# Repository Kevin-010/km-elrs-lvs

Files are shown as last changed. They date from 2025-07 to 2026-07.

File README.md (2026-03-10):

# km-elrs-lvs
A 2.4ghz ExpressLRS-compatible PWM receiver with integrated cell monitoring. KiCad project and related files.

This was created as a personal project to offset having used propreitary radio systems for several years prior (the previous truely usable open standard being PPM/FM): Suddenly (from my perspective) the community has an open source radio system and it also happens to be the best performing? I had to have one, so I made one.
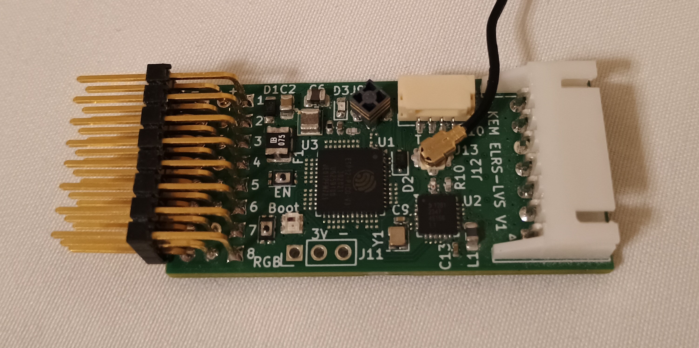
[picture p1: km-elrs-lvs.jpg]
receiver photo

Specs:
- ESP32 (PICO-V3) processor
- SX1280/1281 telemetry radio (direct 1x1, +12.5dBm) anything fancier isn't necessary for outdoor los on a small/medium plane (but more importantly would have been less likely to succeed when hand built)
- 1-3s (3.0-17v) input/servo power, with external brownout detector (the esp builtin one is problematic)
- 8 Channel PWM output, on standard servo pin headers
- JST GH CRSF/Serial/programming connector (similar to radiomaster cables)
- 7 channel voltage sense connector, measuring -5 to +35v (for 2-6s standard lipo balance plugs)

This not a beginner soldering project.  It is built similarly to most RC hardware - double sided with (almost) minimal compoent sizes crammed as close as possible to each other to save size and weight.  That said, it can be assembled by hand - I had no significant issues, although I recommend using at least a paste stencil.

The Wifi (ceramic tower) and ELRS (u.fl) footprints are made more interchangable for experimental purposes. As of version 1, the CRSF connector pinout is non-standard, due to an oversight (I thought it was downside up when I copied it from radiomaster's cable example). There are many test/cut points that could be removed to save space on a version 2 (none of the cut points were necessary, which is a great success, and why it's stuck at the first version)

Version 2 (Not yet tested) removes the test points, moves all components to the front side, fixes the CRSF pinout to match radiomaster cables, and uses larger clearances to allow a slightly cheaper pcb process.

Despite this project being built mostly a cathartic exercise, this has the unique (as of writing) feature of monitoring individual lithium cell voltages integrated into the receiver. This is the most common telemetry item I personally use on aircraft - Having it integrated, in addition to the weight/size reduction, is intended to increase the durability of combat aircraft (on which the cell sensor and interconnect is a common failure point), and otherwise reduce the chance for an aircraft to be missing its sensor. The cost is also theoretically lower than the equivalent two devices, since this only requires hardware integrated into the receiver cpu, but i'd have to sell them for that to actually make sense. This feature currently requires a small amount of custom software, see related repository (TODO LINK HERE).

Some footprints are Borrowed from other public hardware examples:
- https://github.com/crteensy/ELRS-8285-1280-5xPWM.git 
- https://github.com/AnyLeaf/elrs-hardware.git

To build firmware images for this and similar unsupported hardware, one can add an entry to ExpressLRS/targets/targets.json , after which platformio or elrs configurator in local mode can be used.
```
"km_lvs": {
                "product_name": "Kevin LVS 2.4GHz 8xPWM RX",
                "lua_name": "KM LVS",
                "layout_file": "elrs-lvs.json",
                "upload_methods": ["uart", "wifi"],
                "min_version": "3.3.0",
                "platform": "esp32",
                "firmware": "Unified_ESP32_2400_RX"
            },
```

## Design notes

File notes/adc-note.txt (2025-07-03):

            "km_lvs": {
                "product_name": "Kevin LVS 2.4GHz 8xPWM RX",
                "lua_name": "KM LVS",
                "layout_file": "elrs-lvs.json",
                "upload_methods": ["uart", "wifi"],
                "min_version": "3.3.0",
                "platform": "esp32",
                "firmware": "Unified_ESP32_2400_RX"
            },

Adafruit 3x4 Right Angle Male Header - 4 Pack [ADA816] 
https://www.abelectronics.co.uk/p/73/24-pin-8-x-3-right-angle-header

samtec TSW-150-25-F-T-RA
(3x4) TSW-104-25-G-T-RA

adc
real	vs5	lvs6	sim
-6		142	-20.058
-5		142	58.43
-4		172	136.919
-3		248	215.407
-2		327	293.895
-1		405	372.384
0		480	450.872
nc		520	489.274
1		560	529.36
2		640	607.848
3	649	719	686.337
3.3	724		709.884
4	796	797	764.826
5	874	876	843.314
6	953	954	921.802
7	1036	1037	1000
8	1116	1117	1079
9	1195	1196	1157
10	1274	1275	1236
11	1353	1354	1314
12	1438	1438	1393
13	1516	1516	1471
14	1595	1594	1550
15	1671	1672	1628
16	1751	1750	1707
17	1837	1833	1785
18		1910	1864
19		1987	1942
20		2066	2021
21		2143	2099
22		2221	2178
23		2305	2256
24		2387	2335
25		2466	2413
26		2539	2492
27		2611	2570
28		2685	2649
29		2760	2727
30		2835	2806
31		2912	2884

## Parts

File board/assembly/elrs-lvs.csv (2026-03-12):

Reference | Value | Footprint | Qty | Part | Manufacturer | DNP | Alt part number | Digikey | LCSC | Mouser
C4 | 10u | Capacitor_SMD:C_0402_1005Metric | 1 | CL05A106MQ5NUNC | Samsung |  |  | https://www.digikey.com/en/products/detail/samsung-electro-mechanics/CL05A106MQ5NUNC/3887109 | C15525
C7,C8 | 10n | Capacitor_SMD:C_0402_1005Metric | 2 | CL05B103KB5NNNC | Samsung |  |  | https://www.digikey.com/en/products/detail/samsung-electro-mechanics/CL05B103KB5NNNC/3886686 | C15195
C9 | 1n | Capacitor_SMD:C_0402_1005Metric | 1 | KGM05AR71H102KN | Kyocera AVX |  |  | https://www.digikey.com/en/products/detail/kyocera-avx/KGM05AR71H102KN/3661149 | C2168479
C13 | 470n, 10V | Capacitor_SMD:C_0402_1005Metric | 1 | CL05A474KP5NNNC | Samsung |  |  | https://www.digikey.com/en/products/detail/samsung-electro-mechanics/CL05A474KP5NNNC/3886831 | C47339
D4 | WS2812B 2020 | Anyleaf_Shared:LED-WS2812B | 1 | WS2812B-2020 | Multiple |  |  | 1528-4684-ND (Adafruit 4684) | C965555
J13 | U.FL | elrs-lvs:U.FL_Hirose_U.FL-R-SMT-1_Vertical_Molex_47948-0001 | 1 | U.FL-R-SMT-1(80) | Hirose Electric |  |  |  | C88374
L1 | 15u | Inductor_SMD:L_0805_2012Metric | 1 | MLZ2012M150W | TDK |  |  | https://www.digikey.com/en/products/detail/tdk/MLZ2012M150WT000/2465154 | C486333 | 810-MLZ2012M150WT000
U2 | SX1281 | Package_DFN_QFN:QFN-24-1EP_4x4mm_P0.5mm_EP2.6x2.6mm | 1 | SX1281IMLTRT | Semtech |  |  | SX1281IMLTRTTR-ND | C2151551 | 947-SX1281IMLTRT
U3 | TPSM82901SISR | elrs-lvs:uSIP11_SIS_TEX | 1 | TPSM82901SISR | Texas Instruments |  |  | https://www.digikey.com/en/products/detail/texas-instruments/TPSM82901SISR/17394938 | C6290581
U4 | 2450FM07D0034T | Anyleaf_Shared:2450FM07D0034 | 1 | 2450FM07D0034T | Johanson |  | 2450FM07A0029T | 712-1654-2-ND | C2651081 | 609-2450FM07D0034T
Y1 | 52Mhz TCXO | Crystal:Crystal_SMD_2016-4Pin_2.0x1.6mm | 1 | ECS-TXO-20CSMV4-520-AN-TR | ECS Inc. |  |  | 50-ECS-TXO-20CSMV4-520-AN-TRCT-ND | C22434896
C3,C10,C11,C12,C14,C15,C16,C17,C18,C19,C20,C21 | 100n | Capacitor_SMD:C_0402_1005Metric | 12 | CL05A104KA5NNNC | Samsung |  |  | https://www.digikey.com/en/products/detail/samsung-electro-mechanics/CL05A104KA5NNNC/3886701 | C100072
J10 | CF/Prog | Connector_JST:JST_GH_SM04B-GHS-TB_1x04-1MP_P1.25mm_Horizontal | 1 | SM04B-GHS-TB | JST |  |  | https://www.digikey.com/en/products/detail/jst-sales-america-inc/SM04B-GHS-TB/807788 | C189895
D3 | Power | LED_SMD:LED_0603_1608Metric | 1 | LY Q976.01-Q1R2-36-1 | osram |  |  | https://www.digikey.com/en/products/detail/ams-osram-usa-inc/LY-Q976-01-Q1R2-36-1/21556496 | C20562575
F1 | 500ma | Capacitor_SMD:C_1210_3225Metric | 1 | SMD1210B075TF/24 | Yageo |  |  | https://www.digikey.com/en/products/detail/yageo/SMD1210B075TF-24/15212934 | C634245
R1,R13 | 10k | Resistor_SMD:R_0402_1005Metric | 2 | AC0402JR-0710KL | Yageo |  |  | https://www.digikey.com/en/products/detail/yageo/AC0402JR-0710KL/5895571 | C144731
R14 | 470 | Resistor_SMD:R_0402_1005Metric | 1 | AC0402JR-07470RL | Yageo |  |  | https://www.digikey.com/en/products/detail/yageo/AC0402JR-07470RL/5895678 | C144711
R2 | 40.2k | Resistor_SMD:R_0402_1005Metric | 1 | AC0402FR-0740K2L | Yageo |  |  | https://www.digikey.com/en/products/detail/yageo/AC0402FR-0740K2L/5895346 | C144760
R3,R15,R16,R17,R18,R19,R20,R21,R22,R47,R48 | 100 | Resistor_SMD:R_0402_1005Metric | 11 | AC0402JR-07100RL | Yageo |  |  | https://www.digikey.com/en/products/detail/yageo/AC0402JR-07100RL/5895570 | C138288
R10,R31,R32,R33,R34,R35,R36,R37,R38 | 270k | Resistor_SMD:R_0402_1005Metric | 9 | RC0402FR-07270KL | Yageo |  |  | https://www.digikey.com/en/products/detail/yageo/RC0402FR-07270KL/726575 | C163475
R23,R24,R25,R26,R27,R28,R29,R30 | 470k | Resistor_SMD:R_0402_1005Metric | 8 | RC0402DR-07470KL | Yageo |  |  | https://www.digikey.com/en/products/detail/yageo/RC0402DR-07470KL/5917402 | C4001349
R39,R40,R41,R42,R43,R44,R45,R46 | 47k | Resistor_SMD:R_0402_1005Metric | 8 | RC0402FR-0747KL | Yageo |  |  | https://www.digikey.com/en/products/detail/yageo/RC0402FR-0747KL/726616 | C93943
U1 | ESP32-PICO-V3 | Package_DFN_QFN:QFN-48-1EP_7x7mm_P0.5mm_EP5.3x5.3mm | 1 | ESP32-PICO-V3 | Espressif |  |  | https://www.digikey.com/en/products/detail/espressif-systems/ESP32-PICO-V3/11613122 | C967022 | 356-ESP32-PICO-V3
SW1,SW2 | SW_SPST | elrs-lvs:SO4_SW_1563-R66-8005_MIT | 2 | R-668048 | Mitsumi |  |  | https://www.digikey.com/en/products/detail/mitsumi-electric-company-ltd/R-668048/11591275 | C4364937
J9 | Little Tower | elrs-lvs:Molex_47948-0001_U.FL_Hirose_U.FL-R-SMT-1_Vertical | 1 | 47948-0001 | Molex |  |  | https://www.digikey.com/en/products/detail/molex/0479480001/2683663?s=N4IgTCBcDaICwHYCccAcBaADNgjCAugL5A | C152351 | 538-47948-0001
C1 | 1u | Capacitor_SMD:C_0402_1005Metric | 1 | CL05A105MQ5NNNC | Samsung |  |  | https://www.digikey.com/en/products/detail/samsung-electro-mechanics/CL05A105MQ5NNNC/3886893 | C318573
C2 | 10u | Capacitor_SMD:C_0805_2012Metric | 1 | GRJ21BR61E106KE01K | Murata |  |  | https://www.digikey.com/en/products/detail/murata-electronics/GRJ21BR61E106KE01K/10705983 | C5646740
C6 | 22u | Capacitor_SMD:C_0805_2012Metric | 1 | C2012X7S1A226M125AC | TDK |  |  | https://www.digikey.com/en/products/detail/tdk-corporation/C2012X7S1A226M125AC/3951796 | C2167548
D1 | 17v | elrs-lvs:US2H_TOS | 1 | CUHZ16V,H3F | Toshiba |  |  | https://www.digikey.com/en/products/detail/toshiba-semiconductor-and-storage/CUHZ16V-H3F/15857862 | C7236804
D2 | 3.3v | Diode_SMD:D_SOD-323 | 1 | PJGBLC03-AU_R1_000A1 | Panjit |  |  | https://www.digikey.com/en/products/detail/panjit-international-inc/PJGBLC03-AU-R1-000A1/15798010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 | C6951951

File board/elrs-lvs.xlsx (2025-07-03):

Reference | Value | Footprint | Qty | Part | Manufacturer | DNP | Digikey | LCSC | Mouser | Pack Qty | Packs for 20 | Pack Cost | Unit Cost | Ordered Mouser SO 269743228 | Ordered Digikey
C1 | 1u | Capacitor_SMD:C_0402_1005Metric | 1 | CL05A105MQ5NNNC | Samsung |  | https://www.digikey.com/en/products/detail/samsung-electro-mechanics/CL05A105MQ5NNNC/3886893 |  |  | 1 | 20 | 0.012 | 0.012 |  | 100
C2 | 10u | Capacitor_SMD:C_0805_2012Metric | 1 | GRJ21BR61E106KE01K | Murata |  | https://www.digikey.com/en/products/detail/murata-electronics/GRJ21BR61E106KE01K/10705983 |  |  | 1 | 20 | 0.137 | 0.137 |  | 50
C3,C10,C11,C12,C14,C15,C16,C17,C18,C19,C20,C21 | 100n | Capacitor_SMD:C_0402_1005Metric | 12 | CL05A104KA5NNNC | Samsung |  | https://www.digikey.com/en/products/detail/samsung-electro-mechanics/CL05A104KA5NNNC/3886701 | C1525 |  | 1 | 240 | 0.0042 | 0.0042 |  | 1000
C4 | 10u | Capacitor_SMD:C_0402_1005Metric | 1 | CL05A106MQ5NUNC | Samsung |  | https://www.digikey.com/en/products/detail/samsung-electro-mechanics/CL05A106MQ5NUNC/3887109 | C15525 |  | 1 | 20 | 0.108 | 0.108 |  | 50
C5 | DNP | Capacitor_SMD:C_0402_1005Metric | 1 | DNP |  | DNP |  |  |  | 1 | 20 | 0 | 0
C6 | 22u | Capacitor_SMD:C_0805_2012Metric | 1 | C2012X7S1A226M125AC | TDK |  | https://www.digikey.com/en/products/detail/tdk-corporation/C2012X7S1A226M125AC/3951796 |  |  | 1 | 20 | 0.416 | 0.416 |  | 50
C7,C8 | 10n | Capacitor_SMD:C_0402_1005Metric | 2 | CL05B103KB5NNNC | Samsung |  | https://www.digikey.com/en/products/detail/samsung-electro-mechanics/CL05B103KB5NNNC/3886686 | C15195 |  | 1 | 40 | 0.014 | 0.014 |  | 100
C9 | 1n | Capacitor_SMD:C_0402_1005Metric | 1 | KGM05AR71H102KN | Kyocera AVX |  | https://www.digikey.com/en/products/detail/kyocera-avx/KGM05AR71H102KN/3661149 | C1523 |  | 1 | 20 | 0.01 | 0.01 |  | 100
C13 | 470n, 10V | Capacitor_SMD:C_0402_1005Metric | 1 | CL05A474KP5NNNC | Samsung |  | https://www.digikey.com/en/products/detail/samsung-electro-mechanics/CL05A474KP5NNNC/3886831 | C47339 |  | 1 | 20 | 0.05 | 0.05 |  | 100
C22,C23 | DNP | elrs-lvs:R_0201_0603_NP | 2 | DNP |  |  |  |  |  | 1 | 40 | 0 | 0
D1 | 17v | elrs-lvs:US2H_TOS | 1 | CUHZ16V,H3F | Toshiba |  | https://www.digikey.com/en/products/detail/toshiba-semiconductor-and-storage/CUHZ16V-H3F/15857862 |  |  | 1 | 20 | 0.31 | 0.31 |  | 20
D2 | 3.3v | Diode_SMD:D_SOD-323 | 1 | PJGBLC03C-AU_R1_000A1 | Panjit |  | https://www.digikey.com/en/products/detail/panjit-international-inc/PJGBLC03C-AU-R1-000A1/15797697 |  |  | 1 | 20 | 0.345 | 0.345 |  | 20
D3 | Power | LED_SMD:LED_0603_1608Metric | 1 | LY Q976.01-Q1R2-36-1 | osram |  | https://www.digikey.com/en/products/detail/ams-osram-usa-inc/LY-Q976-01-Q1R2-36-1/21556496 |  |  | 1 | 20 | 0.115 | 0.115 |  | 100
D4 | WS2812B | Anyleaf_Shared:LED-WS2812B | 1 | 4684 | Adafruit |  | 1528-4684-ND | C965555 |  | 10 | 2 | 3.95 | 0.395 | 2
F1 | 500ma | Capacitor_SMD:C_1210_3225Metric | 1 | SMD1210B075TF/24 | Yageo |  | https://www.digikey.com/en/products/detail/yageo/SMD1210B075TF-24/15212934 |  |  | 1 | 20 | 0.119 | 0.119 |  | 20
J1,J2,J3,J4,J5,J6,J7,J8 | PWM | Connector_PinHeader_2.54mm:PinHeader_1x03_P2.54mm_Vertical | 8 | TSW-104-25-G-T-RA | Samtec |  | https://www.digikey.com/en/products/detail/samtec-inc/TSW-104-25-G-T-RA/7864909 |  |  | 4 | 40 | 1.53 | 0.3825 |  | 50
J10 | CF/Prog | Connector_JST:JST_GH_SM04B-GHS-TB_1x04-1MP_P1.25mm_Horizontal | 1 | SM04B-GHS-TB | JST |  | https://www.digikey.com/en/products/detail/jst-sales-america-inc/SM04B-GHS-TB/807788 | C189895 |  | 1 | 20 | 0.389 | 0.389 |  | 20
J11 | Holes | Connector_PinHeader_2.54mm:PinHeader_1x03_P2.54mm_Vertical | 1 | DNP |  |  |  |  |  | 1 | 20 | 0 | 0
J12 | Balance | Connector_JST:JST_XH_S7B-XH-A-1_1x07_P2.50mm_Horizontal | 1 | S7B-XH-A-1 | JST |  | https://www.digikey.com/en/products/detail/jst-sales-america-inc/S7B-XH-A-1/9961926 |  |  | 1 | 20 | 0.422 | 0.422 |  | 20
J13 | U.FL | elrs-lvs:U.FL_Hirose_U.FL-R-SMT-1_Vertical_Molex_47948-0001 | 1 | U.FL-R-SMT-1(80) | Hirose Electric |  |  | C88374 |  | 1 | 20 | 1.114 | 1.114 | 20
L2 | JP | elrs-lvs:R_0201_0603_JP | 1 | DNP |  |  |  |  |  | 1 | 20 | 0 | 0
R1,R13 | 10k | Resistor_SMD:R_0402_1005Metric | 2 | AC0402JR-0710KL | Yageo |  | https://www.digikey.com/en/products/detail/yageo/AC0402JR-0710KL/5895571 |  |  | 1 | 40 | 0.016 | 0.016 |  | 100
R2 | 40.2k | Resistor_SMD:R_0402_1005Metric | 1 | AC0402FR-0740K2L | Yageo |  | https://www.digikey.com/en/products/detail/yageo/AC0402FR-0740K2L/5895346 |  |  | 1 | 20 | 0.019 | 0.019 |  | 100
R3,R4,R5,R6,R7,R8,R9,R11,R12 | DNP | Resistor_SMD:R_0402_1005Metric | 9 | DNP |  | DNP |  |  |  | 1 | 180 | 0 | 0
R10,R31,R32,R33,R34,R35,R36,R37,R38 | 270k | Resistor_SMD:R_0402_1005Metric | 9 | RC0402FR-07270KL | Yageo |  | https://www.digikey.com/en/products/detail/yageo/RC0402FR-07270KL/726575 |  |  | 1 | 180 | 0.0073 | 0.0073 |  | 500
R14 | 470 | Resistor_SMD:R_0402_1005Metric | 1 | AC0402JR-07470RL | Yageo |  | https://www.digikey.com/en/products/detail/yageo/AC0402JR-07470RL/5895678 |  |  | 1 | 20 | 0.016 | 0.016 |  | 100
R15,R16,R17,R18,R19,R20,R21,R22,R47,R48 | 100 | Resistor_SMD:R_0402_1005Metric | 10 | AC0402JR-07100RL | Yageo |  | https://www.digikey.com/en/products/detail/yageo/AC0402JR-07100RL/5895570 |  |  | 1 | 200 | 0.0058 | 0.0058 |  | 500
R23,R24,R25,R26,R27,R28,R29,R30 | 470k | Resistor_SMD:R_0402_1005Metric | 8 | RC0402DR-07470KL | Yageo |  | https://www.digikey.com/en/products/detail/yageo/RC0402DR-07470KL/5917402 |  |  | 1 | 160 | 0.0196 | 0.0196 |  | 500
R39,R40,R41,R42,R43,R44,R45,R46 | 47k | Resistor_SMD:R_0402_1005Metric | 8 | RC0402FR-0747KL | Yageo |  | https://www.digikey.com/en/products/detail/yageo/RC0402FR-0747KL/726616 |  |  | 1 | 160 | 0.0073 | 0.0073 |  | 500
SW1,SW2 | SW_SPST | elrs-lvs:SO4_SW_1563-R66-8005_MIT | 2 | R-668048 | Mitsumi |  | https://www.digikey.com/en/products/detail/mitsumi-electric-company-ltd/R-668048/11591275 |  |  | 1 | 40 | 0.269 | 0.269 |  | 25
TP2,TP3,TP4,TP5,TP6,TP7,TP8,TP9,TP10,TP11,TP12,TP13,TP14,TP15,TP16,TP18,TP19,TP20 | TP | elrs-lvs:TestPoint_Pad_D0.25mm | 18 | DNP |  |  |  |  |  | 1 | 360 | 0 | 0
U3 | TPSM82901SISR | elrs-lvs:uSIP11_SIS_TEX | 1 | TPSM82901SISR | Texas Instruments |  | https://www.digikey.com/en/products/detail/texas-instruments/TPSM82901SISR/17394938 |  |  | 1 | 20 | 3.534 | 3.534 |  | 10
Y1 | 52Mhz TCXO | Crystal:Crystal_SMD_2016-4Pin_2.0x1.6mm | 1 | ECS-TXO-20CSMV4-520-AN-TR | ECS Inc. |  | 50-ECS-TXO-20CSMV4-520-AN-TRCT-ND |  |  | 1 | 20 | 1.52 | 1.52 |  | 20
U1 | ESP32-PICO-V3 | Package_DFN_QFN:QFN-48-1EP_7x7mm_P0.5mm_EP5.3x5.3mm | 1 | ESP32-PICO-V3 | Espressif |  |  |  | 356-ESP32-PICO-V3 | 1 | 20 | 2.48 | 2.48 | 10
J9 | Little Tower | elrs-lvs:Molex_47948-0001_U.FL_Hirose_U.FL-R-SMT-1_Vertical | 1 | 47948-0001 | Molex |  |  |  | 538-47948-0001 | 1 | 20 | 1.67 | 1.67 | 20
U2 | SX1281 | Package_DFN_QFN:QFN-24-1EP_4x4mm_P0.5mm_EP2.6x2.6mm | 1 | SX1281IMLTRT | Semtech |  | SX1281IMLTRTTR-ND | C125969 | 947-SX1281IMLTRT | 1 | 20 | 5.28 | 5.28 | 10
U4 | 2450FM07D0034T | Anyleaf_Shared:2450FM07D0034 | 1 | 2450FM07D0034T | Johanson |  | 712-1654-2-ND |  | 609-2450FM07D0034T | 1 | 20 | 0.247 | 0.247 | 100
L1 | 15u | Inductor_SMD:L_0805_2012Metric | 1 | MLZ2012M150W | TDK |  |  | C486333 | 810-MLZ2012M150WT000 | 1 | 20 | 0.078 | 0.078 | 100
PCB |  |  |  |  | JLC |  |  |  |  | 1 | 20 | 4.8 | 4.8
 |  |  |  |  |  |  |  |  |  |  |  |  | 24.3117

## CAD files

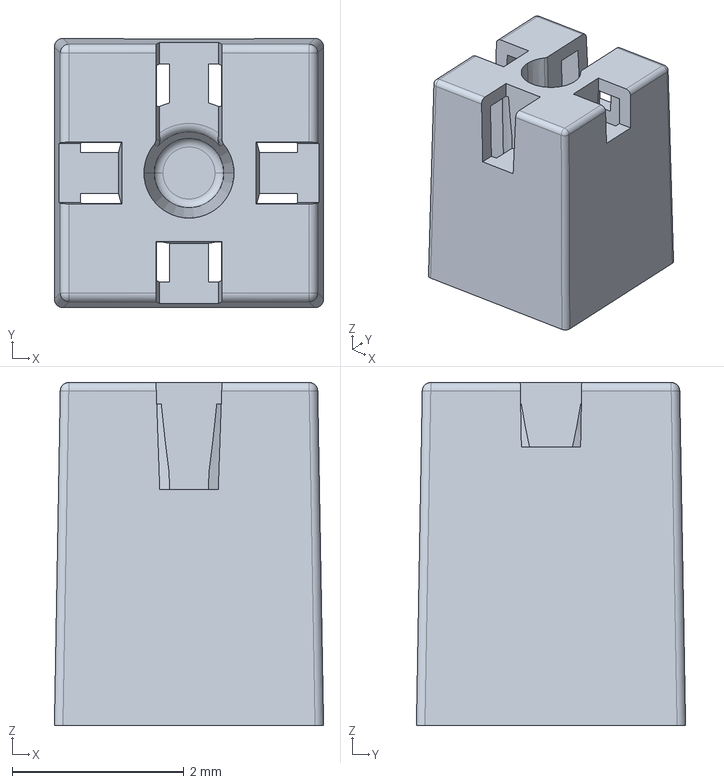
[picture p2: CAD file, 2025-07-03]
board/3d_pwm5/479480001.stp
3.14 x 3.14 x 4.00 mm

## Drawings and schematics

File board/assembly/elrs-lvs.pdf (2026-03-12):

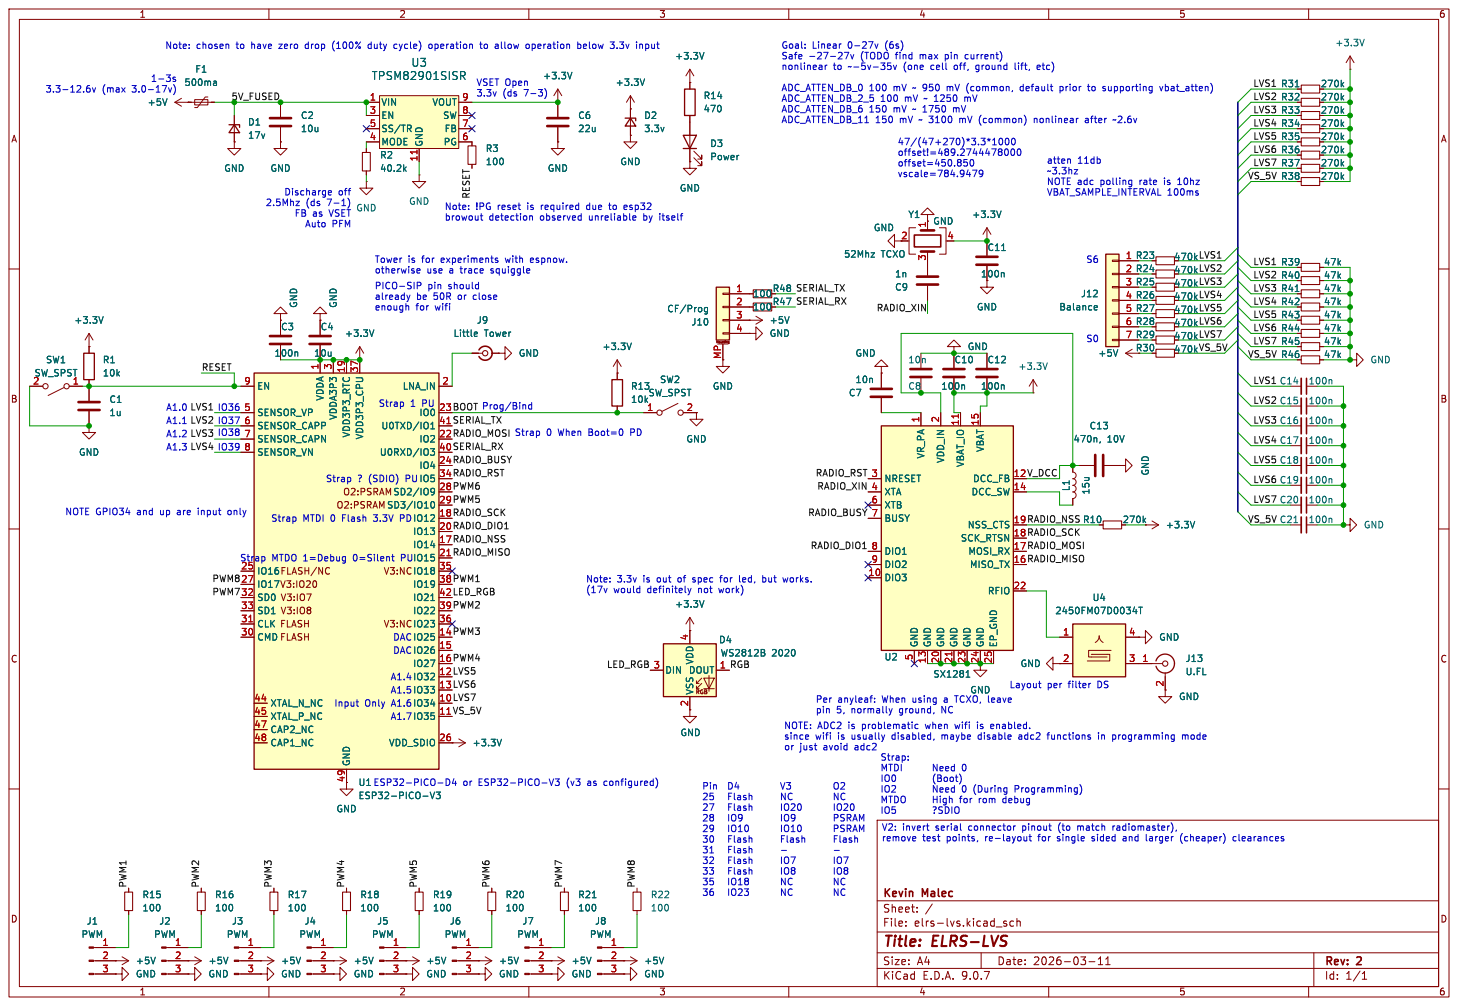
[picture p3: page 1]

2 GND 20 GND 21 VBAT_IO 11 GND 23 VBAT 15 GND 24 EP_GND 25 DCC_FB 12 DCC_SW 14 NSS_CTS 19 SCK_RTSN 18 MOSI_RX 17 MISO_TX 16 RFIO 22 +5VR48 100 R47 100 SW2 SW_SPST
J10 CF/Prog R13

already be 50R or close
enough for wifi Strap 1 PU

2 GND 20 GND 21 VBAT_IO 11 GND 23 VBAT 15 GND 24 EP_GND 25 DCC_FB 12 DCC_SW 14 NSS_CTS 19 SCK_RTSN 18 MOSI_RX 17 MISO_TX 16 RFIO 22 U2 SX1281 GND

Layout per filter DS

Per anyleaf: When using a TCXO, leave

Id: 1/1 Title: ELRS-LVS

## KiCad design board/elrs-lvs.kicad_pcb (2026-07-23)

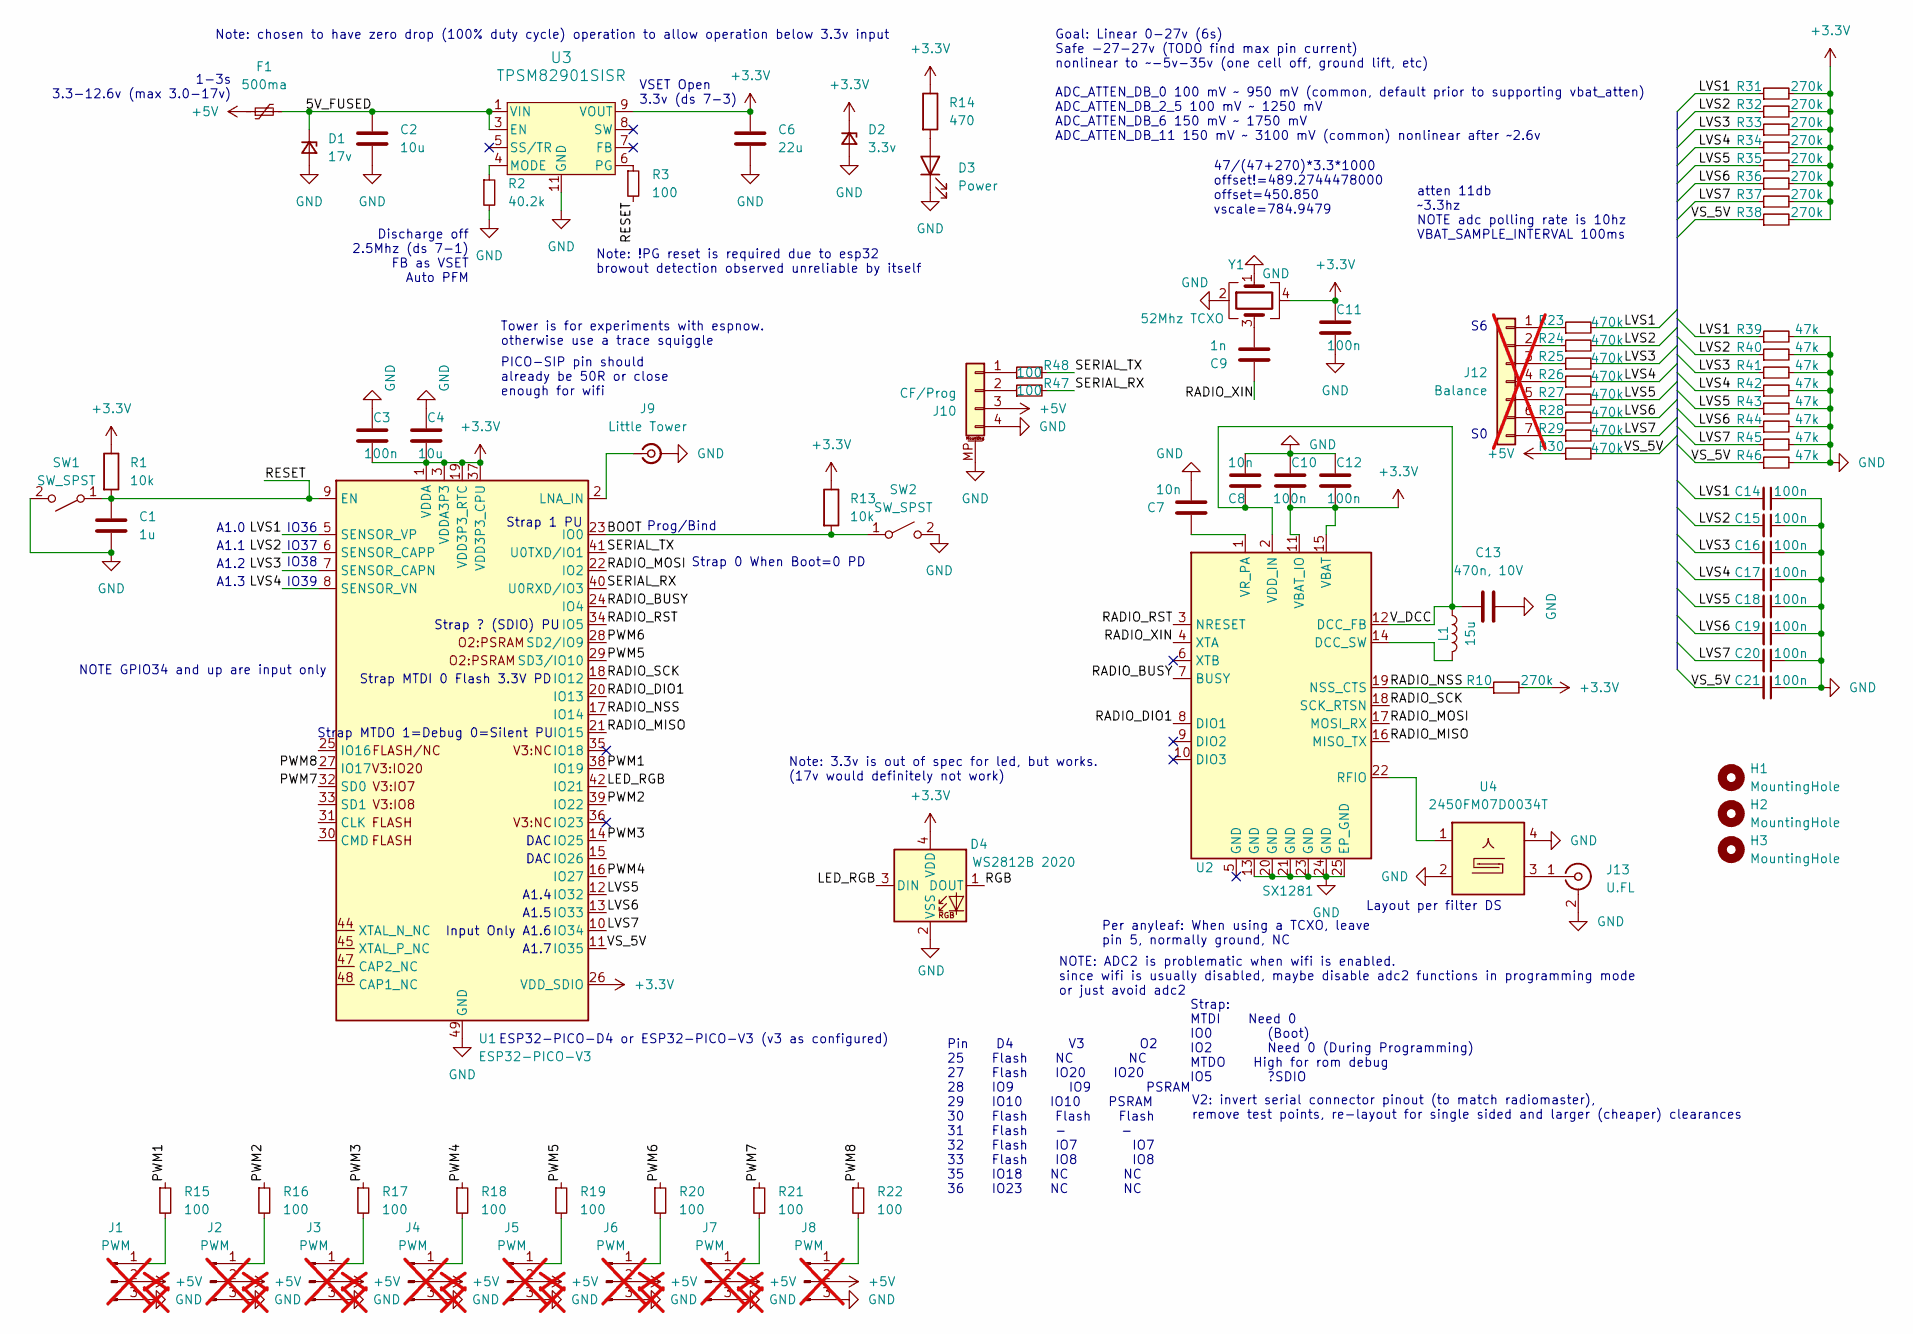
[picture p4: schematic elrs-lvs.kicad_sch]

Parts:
C1: 1u; C_0402_1005Metric; Part CL05A105MQ5NNNC; LCSC C318573
C2: 10u; C_0805_2012Metric; Part GRJ21BR61E106KE01K; LCSC C5646740
C3, C10, C11, C12, C14, C15, C16, C17, C18, C19, C20, C21: 100n; C_0402_1005Metric; Part CL05A104KA5NNNC; LCSC C100072
C4: 10u; C_0402_1005Metric; Part CL05A106MQ5NUNC; LCSC C15525
C6: 22u; C_0805_2012Metric; Part C2012X7S1A226M125AC; LCSC C2167548
C7, C8: 10n; C_0402_1005Metric; Part CL05B103KB5NNNC; LCSC C15195
C9: 1n; C_0402_1005Metric; Part KGM05AR71H102KN; LCSC C2168479
C13: 470n, 10V; C_0402_1005Metric; Part CL05A474KP5NNNC; LCSC C47339
D1: 17v; US2H_TOS; Part CUHZ16V,H3F; LCSC C7236804
D2: 3.3v; D_SOD-323; Part PJGBLC03-AU_R1_000A1; LCSC C6951951
D3: Power; LED_0603_1608Metric; Part LY Q976.01-Q1R2-36-1; LCSC C20562575
D4: WS2812B 2020; LED-WS2812B; Part WS2812B-2020; LCSC C965555
F1: 500ma; C_1210_3225Metric; Part SMD1210B075TF/24; LCSC C634245
H1, H2, H3: MountingHole; MountingHole_JLC
J1, J2, J3, J4, J5, J6, J7, J8: PWM; PinHeader_1x03_P2.54mm_NoSilk; Part TSW-104-25-G-T-RA; not fitted
J9: Little Tower; Molex_47948-0001_U.FL_Hirose_U.FL-R-SMT-1_Vertical; Part 47948-0001; Mouser 538-47948-0001
J10: CF/Prog; JST_GH_SM04B-GHS-TB_1x04-1MP_P1.25mm_Horizontal; Part SM04B-GHS-TB; LCSC C189895
J12: Balance; JST_XH_S7B-XH-A-1_1x07_P2.50mm_Horizontal_Zero_Clearance; Part S7B-XH-A-1; LCSC C491713; not fitted
J13: U.FL; U.FL_Hirose_U.FL-R-SMT-1_Vertical_Molex_47948-0001; Part U.FL-R-SMT-1(80); LCSC C88374
L1: 15u; L_0805_2012Metric; Part MLZ2012M150W; LCSC C486333
R1, R13: 10k; R_0402_1005Metric; Part AC0402JR-0710KL; LCSC C144731
R2: 40.2k; R_0402_1005Metric; Part AC0402FR-0740K2L; LCSC C144760
R3, R15, R16, R17, R18, R19, R20, R21, R22, R47, R48: 100; R_0402_1005Metric; Part AC0402JR-07100RL; LCSC C138288
R10, R31, R32, R33, R34, R35, R36, R37, R38: 270k; R_0402_1005Metric; Part RC0402FR-07270KL; LCSC C163475
R14: 470; R_0402_1005Metric; Part AC0402JR-07470RL; LCSC C144711
R23, R24, R25, R26, R27, R28, R29, R30: 470k; R_0402_1005Metric; Part RC0402DR-07470KL; LCSC C4001349
R39, R40, R41, R42, R43, R44, R45, R46: 47k; R_0402_1005Metric; Part RC0402FR-0747KL; LCSC C93943
SW1, SW2: SW_SPST; SO4_SW_1563-R66-8005_MIT; Part R-668048; LCSC C4364937
U1: ESP32-PICO-V3; QFN-48-1EP_7x7mm_P0.5mm_EP5.3x5.3mm; Part ESP32-PICO-V3; Mouser 356-ESP32-PICO-V3
U2: SX1281; QFN-24-1EP_4x4mm_P0.5mm_EP2.6x2.6mm; Part SX1281IMLTRT; Digikey SX1281IMLTRTTR-ND
U3: TPSM82901SISR; uSIP11_SIS_TEX; Part TPSM82901SISR; LCSC C6290581
U4: 2450FM07D0034T; 2450FM07D0034; Part 2450FM07D0034T; Mouser 609-2450FM07D0034T
Y1: 52Mhz TCXO; Crystal_SMD_2016-4Pin_2.0x1.6mm; Part ECS-TXO-20CSMV4-520-AN-TR; LCSC C22434896

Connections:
+3.3V: C3.2, C4.2, C6.1, C10.2, C11.1, C12.2, D2.1 (K), D4.4 (VDD), R1.1, R10.2, R13.1, R14.1, R31.2, R32.2, R33.2, R34.2, R35.2, R36.2, R37.2, R38.2, U1.1 (VDDA), U1.3 (VDDA3P3), U1.4 (VDDA3P3), U1.19 (VDD3P3_RTC), U1.26 (VDD_SDIO), U1.37 (VDD3P3_CPU), U1.43 (VDDA), U1.46 (VDDA), U2.11 (VBAT_IO), U2.15 (VBAT), U3.9 (VOUT), U3.10 (VOUT), Y1.4
+5V: F1.1, J1.2, J2.2, J3.2, J4.2, J5.2, J6.2, J7.2, J8.2, J10.3, R30.1
/BOOT: R13.2, SW2.1 (A), U1.23 (IO0)
/LED_RGB: D4.3 (DIN), U1.42 (IO21)
/LVS1: C14.2, R23.2, R31.1, R39.1, U1.5 (SENSOR_VP)
/LVS2: C15.2, R24.2, R32.1, R40.1, U1.6 (SENSOR_CAPP)
/LVS3: C16.2, R25.2, R33.1, R41.1, U1.7 (SENSOR_CAPN)
/LVS4: C17.2, R26.2, R34.1, R42.1, U1.8 (SENSOR_VN)
/LVS5: C18.2, R27.2, R35.1, R43.1, U1.12 (IO32)
/LVS6: C19.2, R28.2, R36.1, R44.1, U1.13 (IO33)
/LVS7: C20.2, R29.2, R37.1, R45.1, U1.10 (IO34)
/PWM1: R15.1, U1.38 (IO19)
/PWM2: R16.1, U1.39 (IO22)
/PWM3: R17.1, U1.14 (IO25)
/PWM4: R18.1, U1.16 (IO27)
/PWM5: R19.1, U1.29 (SD3/IO10)
/PWM6: R20.1, U1.28 (SD2/IO9)
/PWM7: R21.1, U1.32 (SD0)
/PWM8: R22.1, U1.27 (IO17)
/RADIO_BUSY: U1.24 (IO4), U2.7 (BUSY)
/RADIO_DIO1: U1.20 (IO13), U2.8 (DIO1)
/RADIO_MISO: U1.21 (IO15), U2.16 (MISO_TX)
/RADIO_MOSI: U1.22 (IO2), U2.17 (MOSI_RX)
/RADIO_NSS: R10.1, U1.17 (IO14), U2.19 (NSS_CTS)
/RADIO_RST: U1.34 (IO5), U2.3 (NRESET)
/RADIO_SCK: U1.18 (IO12), U2.18 (SCK_RTSN)
/RADIO_XIN: C9.2, U2.4 (XTA)
/RESET: C1.1, R1.2, R3.2, SW1.1 (A), U1.9 (EN)
/RGB: D4.1 (DOUT)
/SERIAL_RX: R47.2, U1.40 (U0RXD/IO3)
/SERIAL_TX: R48.2, U1.41 (U0TXD/IO1)
/VS_5V: C21.2, R30.2, R38.1, R46.1, U1.11 (IO35)
/V_DCC: C8.2, C13.1, L1.1, U2.2 (VDD_IN), U2.12 (DCC_FB)
GND: C1.2, C2.2, C3.1, C4.1, C6.2, C7.1, C8.1, C10.1, C11.2, C12.1, C13.2, C14.1, C15.1, C16.1, C17.1, C18.1, C19.1, C20.1, C21.1, D1.2 (A), D2.2 (A), D3.1 (K), D4.2 (VSS), J1.3, J2.3, J3.3, J4.3, J5.3, J6.3, J7.3, J8.3, J9.2 (Ext), J10.4, J10.MP (MountPin), J13.2 (Ext), R2.2, R39.2, R40.2, R41.2, R42.2, R43.2, R44.2, R45.2, R46.2, SW1.2 (B), SW2.2 (B), U1.49 (GND), U2.13 (GND), U2.20 (GND), U2.21 (GND), U2.23 (GND), U2.24 (GND), U2.25 (EP_GND), U3.11 (GND), U4.2, U4.4, Y1.1, Y1.2
unnamed: C9.1, Y1.3
unnamed: D3.2 (A), R14.2
unnamed: J1.1, R15.2
unnamed: J2.1, R16.2
unnamed: J3.1, R17.2
unnamed: J4.1, R18.2
unnamed: J5.1, R19.2
unnamed: J6.1, R20.2
unnamed: J7.1, R21.2
unnamed: J8.1, R22.2
unnamed: J9.1 (In), U1.2 (LNA_IN)
unnamed: J10.1, R48.1
unnamed: J10.2, R47.1
unnamed: J12.1, R23.1
unnamed: J12.2, R24.1
unnamed: J12.3, R25.1
unnamed: J12.4, R26.1
unnamed: J12.5, R27.1
unnamed: J12.6, R28.1
unnamed: J12.7, R29.1
unnamed: J13.1 (In), U4.3
unnamed: L1.2, U2.14 (DCC_SW)
unnamed: U2.22 (RFIO), U4.1
unnamed: C7.2, U2.1 (VR_PA)
unnamed: R2.1, U3.4 (MODE)
unnamed: R3.1, U3.6 (PG)
VIN: C2.1, D1.1 (K), F1.2, U3.1 (VIN), U3.2 (VIN), U3.3 (EN)

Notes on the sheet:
Goal: Linear 0-27v (6s) Safe -27-27v (TODO find max pin current) nonlinear to ~-5v-35v (one cell off, ground lift, etc) ADC_ATTEN_DB_0 100 mV ~ 950 mV (common, default prior to supporting vbat_atten) ADC_ATTEN_DB_2_5 100 mV ~ 1250 mV ADC_ATTEN_DB_6 150 mV ~ 1750 mV ADC_ATTEN_DB_11 150 mV ~ 3100 mV 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
IO37
PICO-SIP pin should already be 50R or close enough for wifi
A1.4
V2: invert serial connector pinout (to match radiomaster), remove test points, re-layout for single sided and larger (cheaper) clearances
VSET Open 3.3v (ds 7-3)
A1.7
IO39
Strap MTDO 1=Debug 0=Silent PU
A1.2
Input Only A1.6
NOTE: ADC2 is problematic when wifi is enabled. since wifi is usually disabled, maybe disable adc2 functions in programming mode or just avoid adc2
IO36
A1.3
Strap 0 When Boot=0 PD
47/(47+270)*3.3*1000 offset!=489.2744478000 offset=450.850 vscale=784.9479
Strap ? (SDIO) PU
Pin D4 V3 O2 25 Flash NC NC 27 Flash IO20 IO20 28 IO9 IO9 PSRAM 29 IO10 IO10 PSRAM 30 Flash Flash Flash 31 Flash - - 32 Flash IO7 IO7 33 Flash IO8 IO8 35 IO18 NC NC 36 IO23 NC NC
Strap MTDI 0 Flash 3.3V PD
IO38
Per anyleaf: When using a TCXO, leave pin 5, normally ground, NC
Note: !PG reset is required due to esp32 browout detection observed unreliable by itself
A1.0
Prog/Bind
Layout per filter DS
Note: chosen to have zero drop (100% duty cycle) operation to allow operation below 3.3v input
Note: 3.3v is out of spec for led, but works. (17v would definitely not work)
Strap: MTDI Need 0 IO0 (Boot) IO2 Need 0 (During Programming) MTDO High for rom debug IO5 ?SDIO
NOTE GPIO34 and up are input only
atten 11db ~3.3hz NOTE adc polling rate is 10hz VBAT_SAMPLE_INTERVAL 100ms
Strap 1 PU
A1.1
Discharge off 2.5Mhz (ds 7-1) FB as VSET Auto PFM
DAC
ESP32-PICO-D4 or ESP32-PICO-V3 (v3 as configured)
Tower is for experiments with espnow. otherwise use a trace squiggle
A1.5
1-3s 3.3-12.6v (max 3.0-17v)

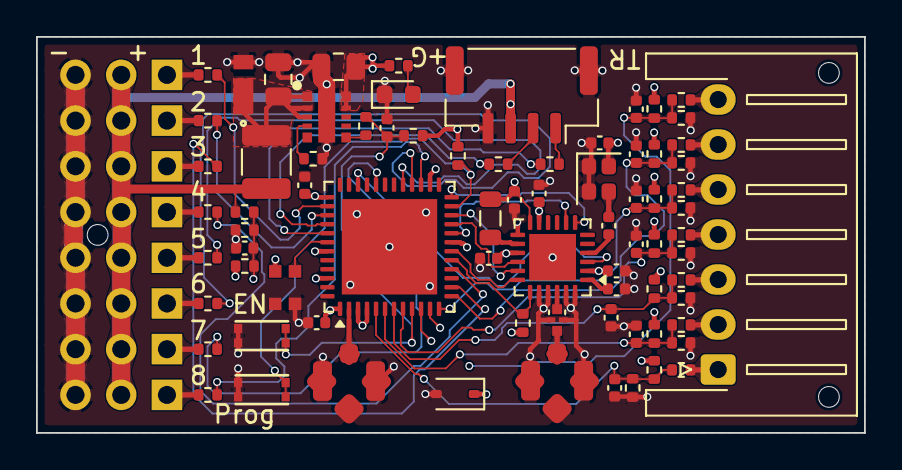
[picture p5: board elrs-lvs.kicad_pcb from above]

Board: 4 copper layers, 46.0 x 22.0 mm, 88 parts (1 on the bottom side), 60 nets.

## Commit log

2025-07-03 Initial project files copy, at V1
    [479480001.stp, adc.ods, adc.tsv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]
2026-03-05 update to kicad version 9 format. no changes.
    [elrs-lvs.kicad_pcb, elrs-lvs.kicad_sch]
2026-03-05 invert serial connector pinout
    [elrs-lvs.kicad_pcb, elrs-lvs.kicad_sch]
2026-03-05 remove dnp options and test points
    [elrs-lvs.kicad_pcb, elrs-lvs.kicad_sch]
2026-03-05 update library footprints
    [elrs-lvs.kicad_pcb]
2026-03-08 initial placement for single sided lower density
    [elrs-lvs.kicad_pcb, elrs-lvs.kicad_sch]
2026-03-10 routing prior to starting over with rotation
    [elrs-lvs.kicad_pcb]
2026-03-10 rotate and initial route
    [elrs-lvs.kicad_pcb]
2026-03-10 export for review
    [elrs-lvs-B_Cu.gbr, elrs-lvs-B_Mask.gbr, elrs-lvs-B_Paste.gbr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]
2026-03-10 more cleanup
    [elrs-lvs.kicad_pcb]
2026-03-12 change D2 to unidirectional, add most lcsc numbers (alternates needed for some parts)
    [elrs-lvs.kicad_pcb, elrs-lvs.kicad_sch]
2026-03-12 label adjustment and some footprint drc fixes
    [elrs-lvs-B_Cu.gbr, elrs-lvs-B_Mask.gbr, elrs-lvs-B_Paste.gbr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]
2026-03-12 mess stuff up for investigating jlc pcba
    [elrs-lvs-B_Cu.gbr, elrs-lvs-B_Mask.gbr, elrs-lvs-B_Paste.gbr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]
